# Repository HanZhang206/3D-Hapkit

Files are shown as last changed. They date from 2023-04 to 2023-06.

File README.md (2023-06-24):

<!-- <div align="center"> -->
# **3D Hapkit**: A Low-Cost, Open-Source, 3-DOF Haptic Device Based on the Delta Parallel Mechanism
<div align="center">
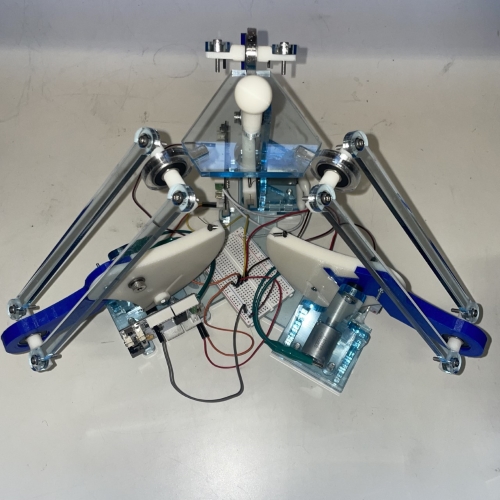
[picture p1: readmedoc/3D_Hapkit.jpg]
3 DOF Hapkit Overview

</div>

The 3D Hapkit is a 3-Degrees-Of-Freedom haptic device that was created as a class project for Haptic Interface Design under Dr. Jeremy Brown in Fall 2022. The 3D Hapkit is based on the [Hapkit 3.0](https://hapkit.stanford.edu/) and was presented as WIP Paper and Demo at [2023 IEEE World Haptics](https://2023.worldhaptics.org/wp-content/uploads/2023/06/1070-doc.pdf). This device is an open-hardware haptic device designed to be low-cost(<$300) and easy to assemble, allowing users to input motions and feel programmed forces in three degrees of freedom. 

Moving forward, the 3D Hapkit will be deployed at the Johns Hopkins University Haptic Interface Design Course in Fall 2023!

<div align="center">


</div>

# **Build One**
## Hardware
<div align="center">
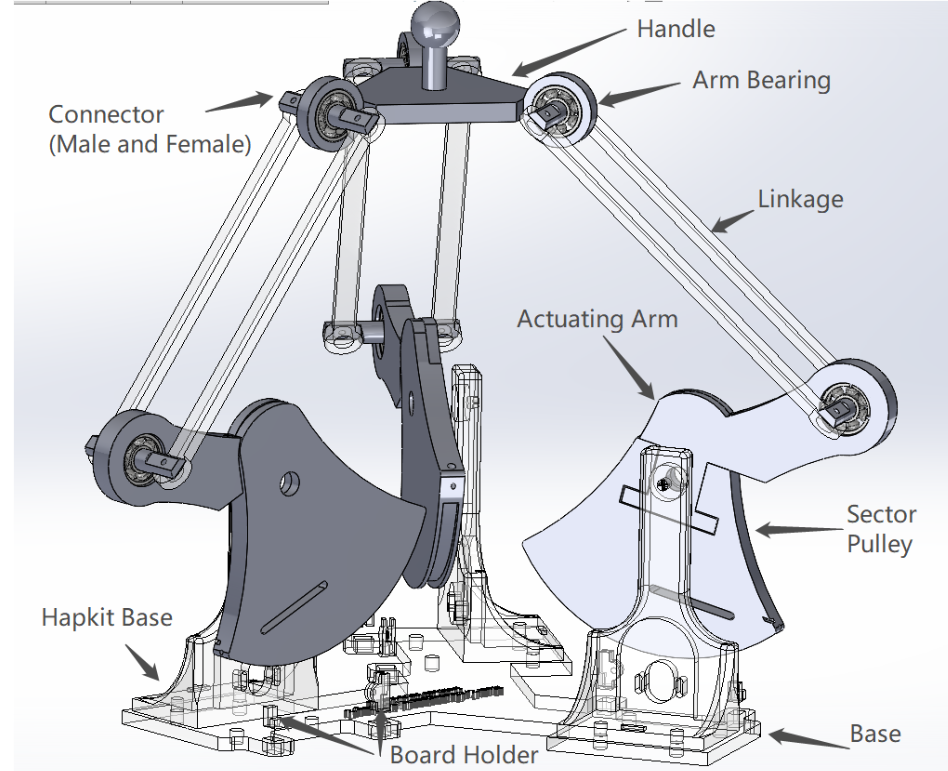
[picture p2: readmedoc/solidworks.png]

</div>  

## Dependency
- [GrabCAD Print Software](https://grabcad.com/print)
- FDM 3D Printer with [ABS filament](https://support.stratasys.com/en/Materials/FDM/ABSplus-P430)/[Soluble Support Material](https://support.stratasys.com/en/Materials/FDM/FDM-Support-Materials)([uPrint SE/uPrint SE Plus](https://support.stratasys.com/en/printers/fdm-legacy/uprint)/[Stratasys F123 Series](https://www.stratasys.com/en/3d-printers/printer-catalog/fdm-printers/f123-series-printers/))
- Laser Cutters([Universal Laser System – VLS6.60](https://www.pdi3d.com/Universal_Laser_VLS6_60_Laser_System_p/ul-vls660.htm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))
- Metric Tap and Die Set(1/4' - 20 & 10-24 & M4)
## Manufacture List
- Parts List: [Here is a parts list with purchase/manufacture information](https://htmlpreview.github.io/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).
- STL files for 3D printing: [Click here to download a zip file of Hapkit STL Files](CAD_and_Manufacturing/3DPrint/3DPrint.zip). Note: Model units are in mm.
- DXF files for laser cutting: [Click here to download a zip file of Hapkit DXF Files](CAD_and_Manufacturing/LaserCut/LaserCut.zip).
- Modifiable SolidWorks files: [Click here to download a zip file of Hapkit SolidWorks Files](CAD_and_Manufacturing/CAD_File/3D-Hapkit.zip). Note: These are only for use with the SolidWorks CAD program.
- Assembly instructions and 3D printing tips: [Here are instructions for assembling your Hapkit into a functional haptic device](readmedoc/assembly.md).

<div align="center">
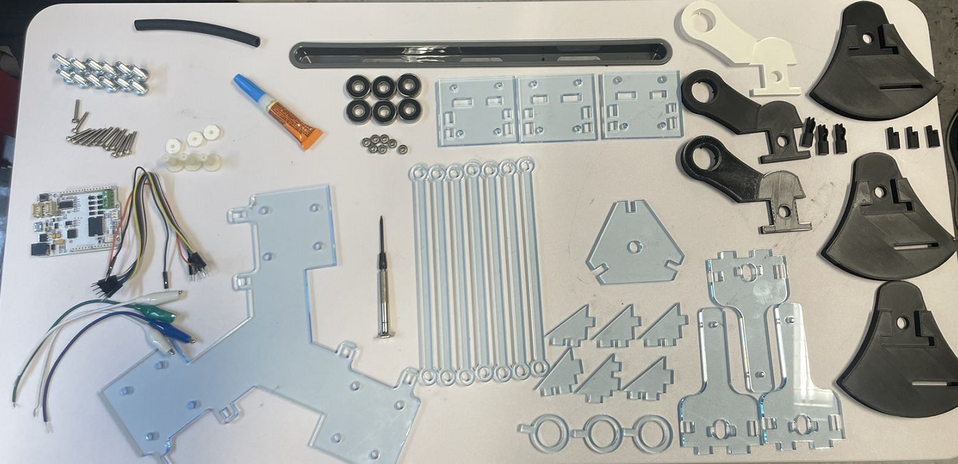
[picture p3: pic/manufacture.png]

</div>

## Electronics 
<div align="center">
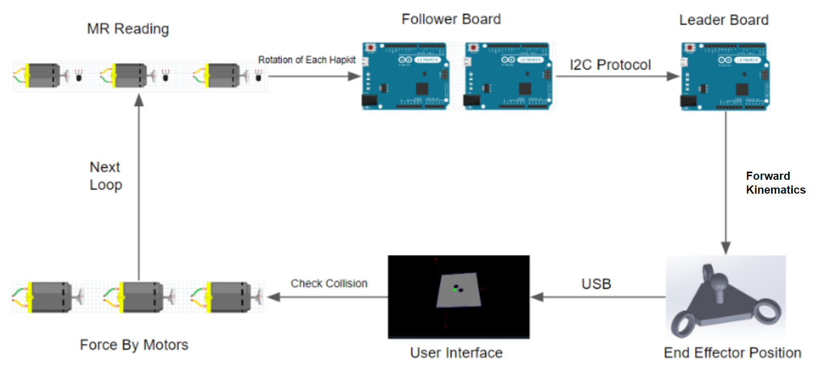
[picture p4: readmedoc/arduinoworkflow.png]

</div>

The electronics of the 3D Hapkit consist of three [Hapkit 3.0s](https://hapkit.stanford.edu/build.html). The Hapkit board can be purchased from [Seeed studio](https://www.seeedstudio.com/depot/hapkit-p-1622.html). It is also possible to manufacture your own PCB by combining an Arduino, motor driver and sensors. Here is a good starting point obtained from Seeed Studio([Files](readmedoc/HapkitSeeedPCB.zip)).

The three boards are communicating using the I2C protocol. We provid sample [Arduino code for follower](3DHapkit_Script/3DHapkit_Follower/3DHapkit_Follower.ino) and [leader](3DHapkit_Script/3DHapkit_Leader/3DHapkit_Learder.ino) to get you started porgramming haptic virtual environments with your 3D Hapkit. The code includes the calculation of forward kinematics and all readings values from sensors.

### To use 
- Connect the ground and I2C pins (A4/A5) of the three boards together.
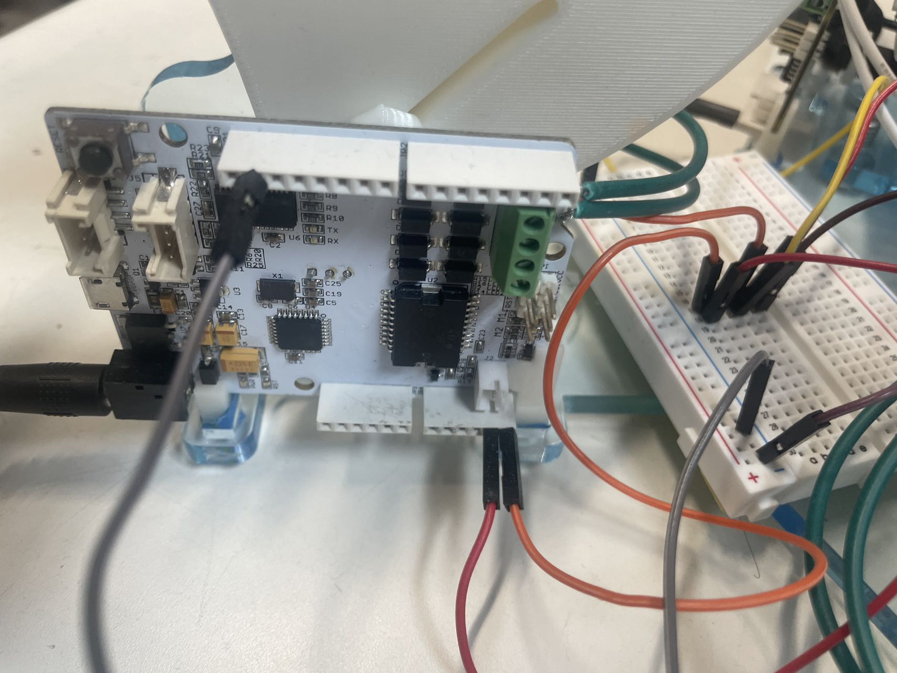
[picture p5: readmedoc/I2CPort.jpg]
  
- Choose one board as the leader and load the script(3DHapkit_Leader.ino).([Arduino IDE Download](https://www.arduino.cc/en/software)).
    - If want to use the serial monitor in the Arduino IDE, comment out **Line 79**(3DHapkit_Leader.ino) in the script:
    ```cpp
  #define PROCESSING 1 //connect to the processing for visualization
    ``` 
- Load the script(3DHapkit_Follower.ino) to two other boards. 
    - In **line 55** (**3DHapkit_Follower.ino**), assign address #8 to follower #1
    ```cpp
  Wire.begin(8);                // join i2c bus with address #8
    ```
    - In **line 58** (**3DHapkit_Follower.ino**), assign address #12 to follower #2
    ```cpp
  Wire.begin(12);                // join i2c bus with address #12
    ```

## Software 
We have created a sample scene for demo purposes. Users are able to control a ball (shown in green) by moving the handle. The ball is rendered in a virtual environment with a virtual surface. Our 3-DOF Hapkit is designed to simulate the virtual surface and render haptic interactions with the surface. Processing ([Download Here](https://processing.org/download)) was used to provide a better visualization.

### To use 
 - Download the [Processing](https://processing.org/download).
 - Open Processing and [deltaProcessing.pde](3DHapkit_Script/deltaProcessing/deltaProcessing.pde).
 - Connect the laptop to the leader board.
 - Check the USB port and change to correct one in **line 38**
     ```cpp
     myPort = new Serial(this, "com5", 115200); //change "com5" based on the local port connection 
      ```
 - Click 'Run'.

<div align="center">
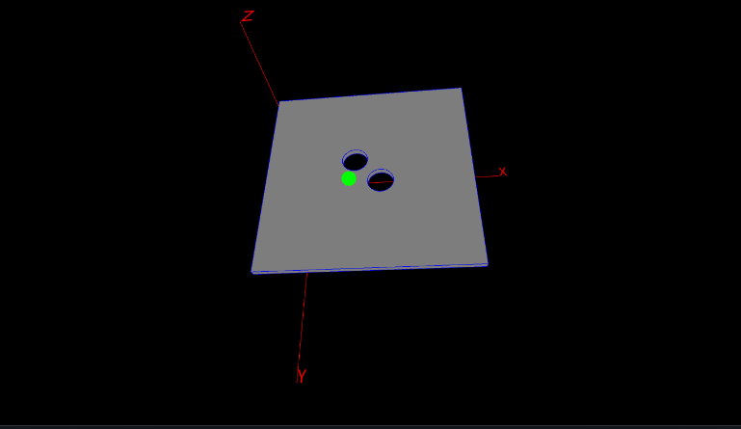
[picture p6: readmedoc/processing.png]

</div>

# **Acknowledgement**
The development and implementation of the 3D Hapkit was supported by the [Haptics and Medical Robotics(HAMR) Laboratory](https://hamr.lcsr.jhu.edu/). Special thanks to Dr. Jeremy Brown for this guidance and invaluable advice.

The 3D Hapkit was made possible by the Hapkit: https://hapkit.stanford.edu/about.html

T. K. Morimoto, P. Blikstein and A. M. Okamura, "[D81] Hapkit: An open-hardware haptic device for online education," 2014 IEEE Haptics Symposium (HAPTICS), Houston, TX, USA, 2014, pp. 1-1, doi: 10.1109/HAPTICS.2014.6775560.

# **Contributors**
 - Han Zhang - MSE in Biomedical Engineering, Johns Hopkins University
 - Jan Bartels - MSE in Robotics, Johns Hopkins University
 - Yuting Zhang - MSE in Computer Science, Johns Hopkins University

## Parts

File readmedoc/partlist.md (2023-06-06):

| **Component** | **3D Model** | **Quanitity** | **Manufacture Method** | **Material** | **Cost** | 
| :-----| :----: | :----: | :----: | :----: | :----: |
| Base | | 1 |Laser Cutter | 15/64" Cast Acrylic | ~ | 
| Linkage |  | 6 |Laser Cutter | 15/64" Cast Acrylic | ~ | 
| Handle |  | 1 |Laser Cutter | 15/64" Cast Acrylic | ~ | 
| 1-Dof Hapkit Base |  | 3 |Laser Cutter | 15/64" Cast Acrylic | ~ | 
| 3D Hapkit Sector Pulley |  | 3 |FDM 3D Printing  | ABS | ~ | 
| Actuating Arm |  | 3 |FDM 3D Printing  | ABS | ~ | 
| 3D Printed Connector(Male) |  | 6 |FDM 3D Printing  | ABS  | ~ | 
| 3D Printed Connector(Female) |  | 6 |FDM 3D Printing  | ABS  | ~ | 
| 3D Printed Tightening Washer |  | 3 |FDM 3D Printing  | ABS  | ~ | 
| 3D Printed Drive Wheel/Magnet Holder |  | 3 |FDM 3D Printing  | ABS  | ~ | 
| Broad Holder 1 |  | 3 |FDM 3D Printing  | ABS  | ~ | 
| Broad Holder 2 |  | 3 |FDM 3D Printing  | ABS  | ~ | 
| Connection Bearing 3mm * 8mm * 4mm |  | 12 |Purchased from [Amazon](https://www.amazon.com/Bearing-Shielded-Bearings-Performance-Effective/dp/B092Z2QB6X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) | Alloy Steel | $9.20 for 20 Pack 623ZZ Ball Bearing | 
| Arm Bearing 8mm * 22mm * 7mm |  | 12 |Purchased from [Amazon](https://www.amazon.com/Industrial-8x22x7mm-Bearings-Pre-Lubricated-Skateboards/dp/B09S5Z5J5L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) | Alloy Steel | 2 * $10.99 (4 Pack 608-2RS Ball Bearing)| 
| Screws (for capstan adjustment) size 4-40, 3/4" length  |  | 3 | Purchased from Mcmaster-Carr(Part ID: 91781A113) | 18-8 Stainless Steel |  $6.78 per pack of 100 | 
| Pan Head Phillips Screws(for Hapkit installation),¼-20 3/4 |  | 12 |Purchased from Mcmaster-Carr(Part ID:91772A540) | 18-8 Stainless Steel | $18.85 per pack of 50 | 
| Pan Head Phillips Screws(for bearing installation),M4 x 0.7mm Thread, 16mm Long |  | 12 |Purchased from Mcmaster-Carr(Part ID:92000A226) | 18-8 Stainless Steel | $10.85 per pack of 50 | 
|Neoprene tubing, 1/4" inner diameter, 3/8" outer diameter, cut to 3/4" length |  | 3 |Purchased from Mcmaster-Carr(Part ID:51075K27) | Neoprene | $12.2 for a 10'-long tube ($1.22 per foot) | 
| Bearing: SAE 863 bronze flanged sleeve bearing |  | 3 |Purchased from Mcmaster-Carr(Part ID: 2938T3) | 863 Iron-Copper | 3 * $0.92 | 
| Stainless Steel Thread-Locking Shoulder Screw, 1/4" Diameter x 5/8" Long Shoulder, 10-24 Thread |  | 3 | Purchased from Mcmaster-Carr(Part ID: 90311A144) | Stainless Steel | 3 * $6.01 | 
| Shaft collar |  | 3 |Purchased from Mcmaster-Carr(Part ID: 9414T6) | Black-oxide steel | 3 * $1.55 | 
| Screws for the motor  |  | 6 |Purchased from Mcmaster-Carr(Part ID: 91735A104) | 316 Stainless Steel | $4.59 For a Pack of 50 | 
| Washers for motor |  | 6 |Purchased from Mcmaster-Carr(Part ID: 92150A101) | Nylon Plastic | $10.20 For a Pack of 100 | 
| Nylon Coated Stainless Steel Wire Rope |  | 3 |Purchased from Mcmaster-Carr(Part ID: 8930T16)| 18-8 Stainless Steel | $10.00 For 25 feet | 
| Zinc - Plated Copper Oval Compression Sleeve |  | 3 |Purchased from Mcmaster-Carr(Part ID: 3898T29) | Zinc-Plated Copper | $2.63 For a Pack of 50 | 
| Zinc -Plated Steel Machine Screw Hex Nut |  | 3 |Purchased from Mcmaster-Carr(Part ID: 90480A005) | Zinc-Plated Copper | $1.05 For a Pack of 100 | 
| Motor |  | 3 |Purchased from Jameco(Part ID: 238473) | Motor | 3 * $5.95 | 
| Magnet |  | 3 |Purchased from Jameco(Part ID: 57295K73) | Alnico | 3 * $2.38 | 
| Magnetoresistive sensor|  | 3 |Purchased from DigiKey (Part ID:568-8399-1-ND) | Magnet Sensor | 3 * $6.73  | 
| Hapkit board |  | 3 |Purchased from Seeed Studio(Part ID :KIT04300M) | Hapkit Board | 3 * $35 | 
| Power supply for Hapkit board |  | 3 |Purchased from Pololu (Part ID: 1471) | Power Supply | 3 * $7.95 | 
| Leads with alligator clips on both ends |  | 3 |Purchased from Mouser(Part ID: 474-CAB-14303) | Alligator Clips | $7.57 | 
| USB cable for communication |  | 1 |Purchased from Monoprice(Part ID: 4867) | Cable  | $1.49 | 

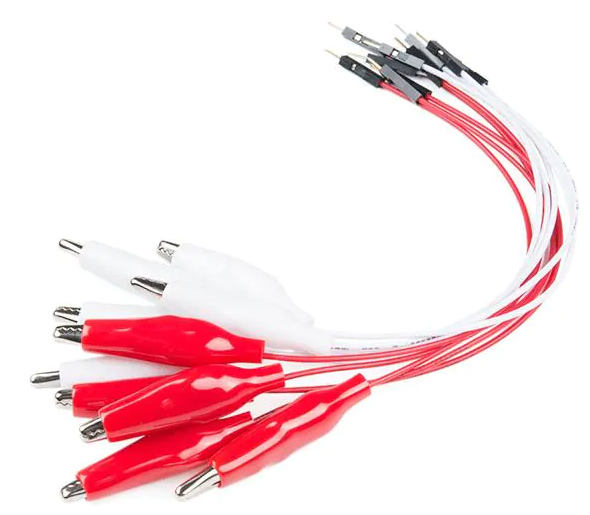
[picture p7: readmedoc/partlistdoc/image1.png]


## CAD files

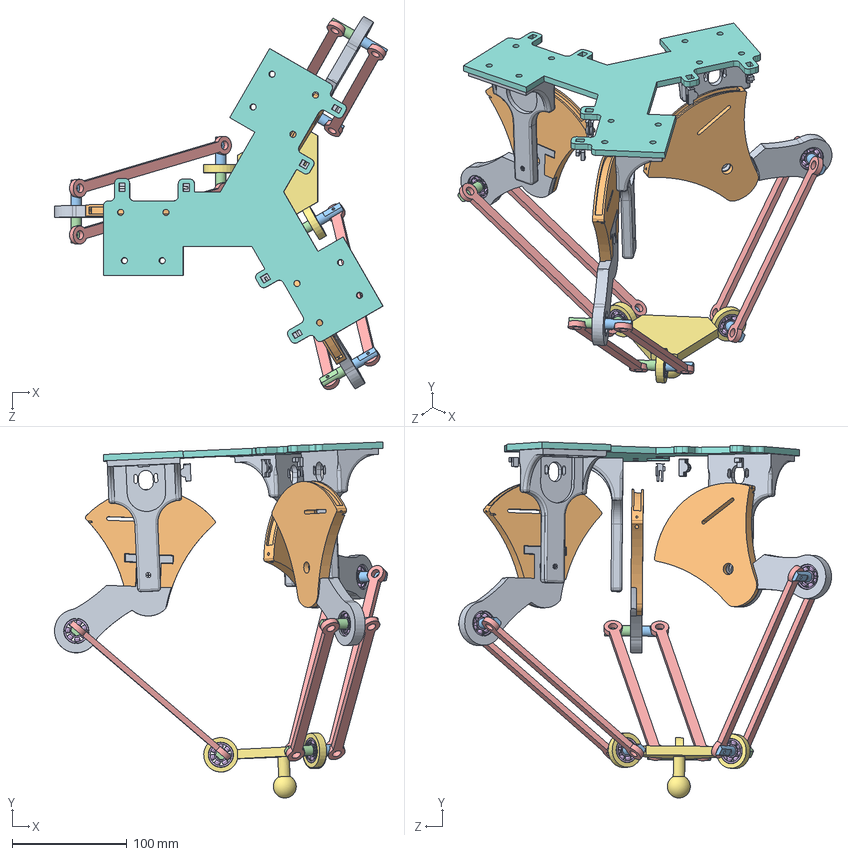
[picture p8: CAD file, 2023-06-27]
CAD_and_Manufacturing/CAD_File/3D-Hapkit.SLDASM
290.2 x 310.1 x 325.1 mm
Hapkit3_0_Base x 3
Hapkit Sector Pulley x 3
Connector_Male x 6
Connector_Female x 6
Linkage x 6
608-2RS.step x 6
handle
base
Actuating Arm x 3

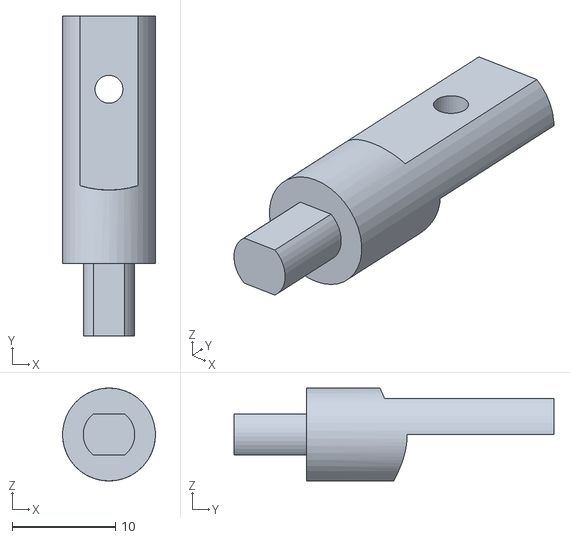
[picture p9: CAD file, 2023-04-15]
CAD_and_Manufacturing/3DPrint/Connector_MaleX6.STL
9.00 x 31.0 x 9.00

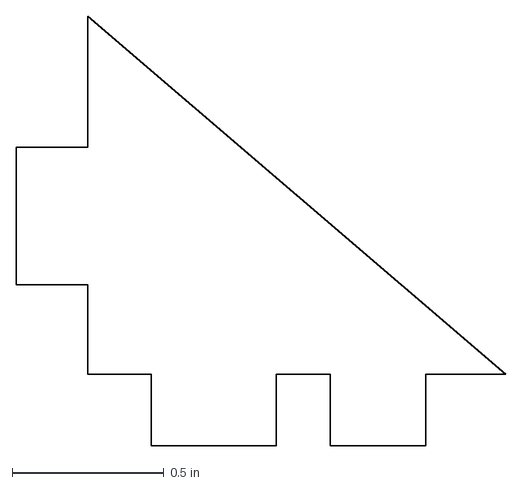
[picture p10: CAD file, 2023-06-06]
CAD_and_Manufacturing/LaserCut/support2X3.DXF
1.61 x 1.42 in

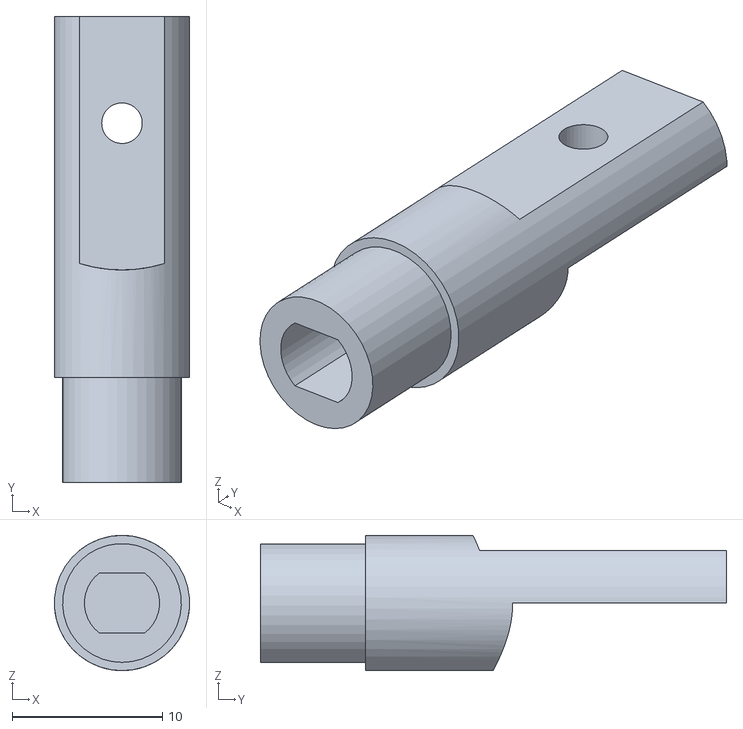
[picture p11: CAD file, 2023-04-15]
CAD_and_Manufacturing/3DPrint/Connector_FemaleX6.STL
9.00 x 31.0 x 9.00

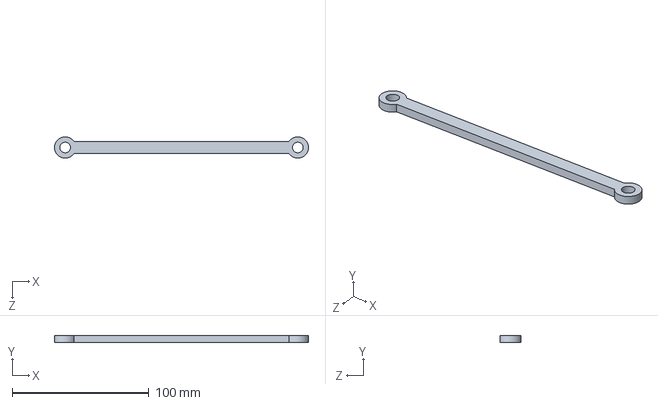
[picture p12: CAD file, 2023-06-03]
CAD_and_Manufacturing/CAD_File/Linkage.SLDPRT
185.6 x 5.00 x 15.6 mm

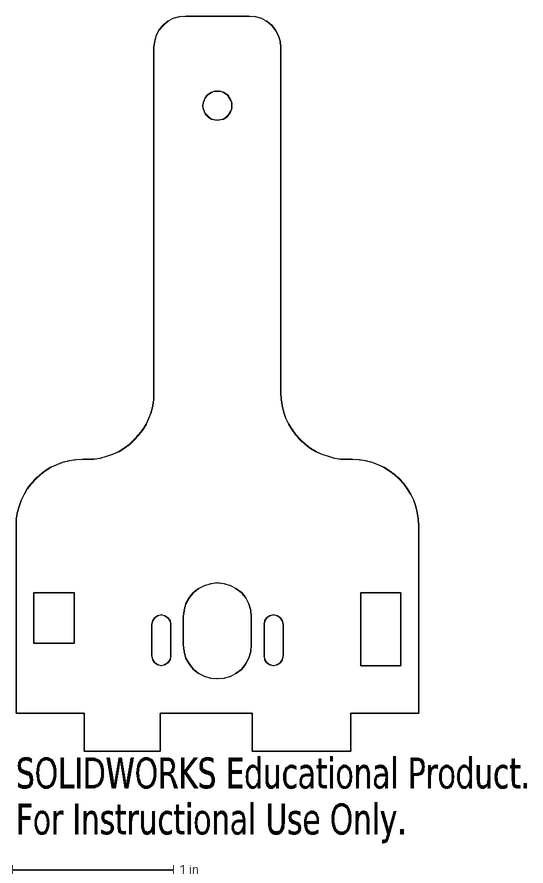
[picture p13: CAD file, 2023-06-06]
CAD_and_Manufacturing/LaserCut/standX3.DXF
SOLIDWORKS Educational Product.
For Instructional Use Only.

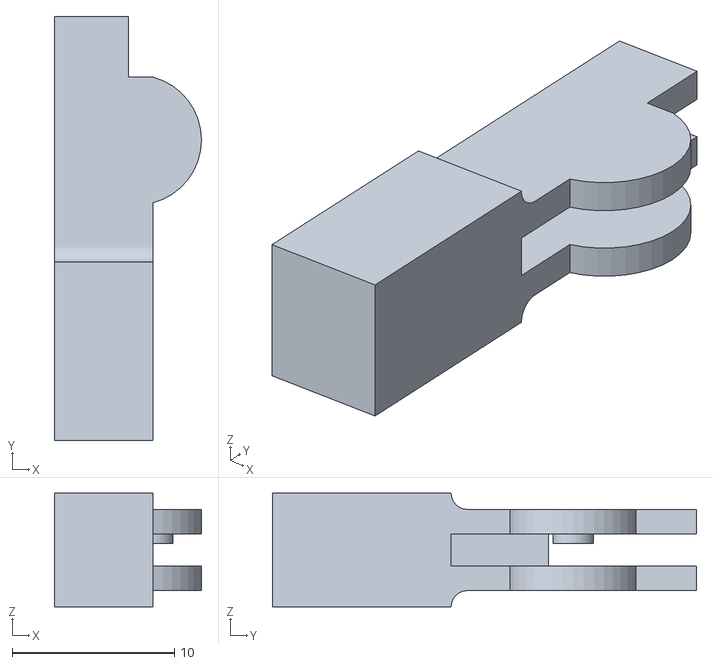
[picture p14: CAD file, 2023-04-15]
CAD_and_Manufacturing/3DPrint/printx_2X3.STL
9.05 x 26.1 x 7.00

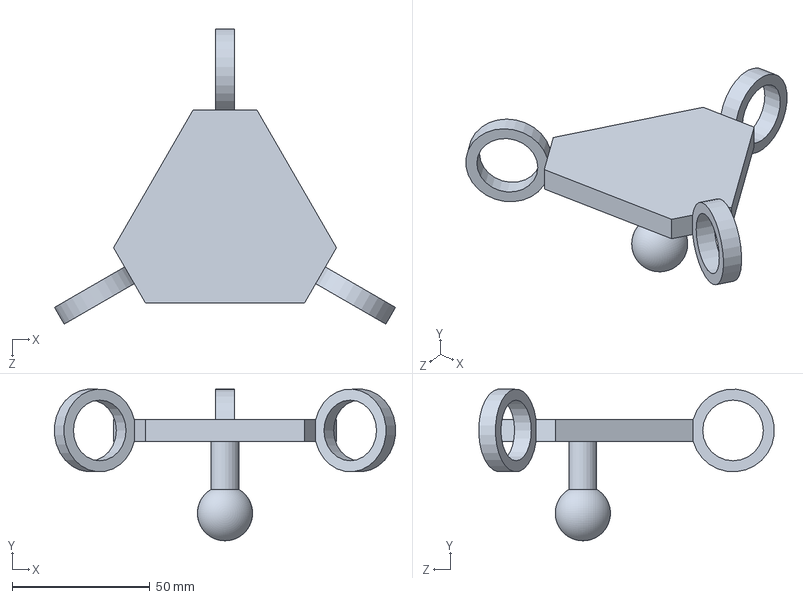
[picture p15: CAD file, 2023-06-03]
CAD_and_Manufacturing/CAD_File/handle.SLDPRT
123.6 x 55.0 x 107.1 mm

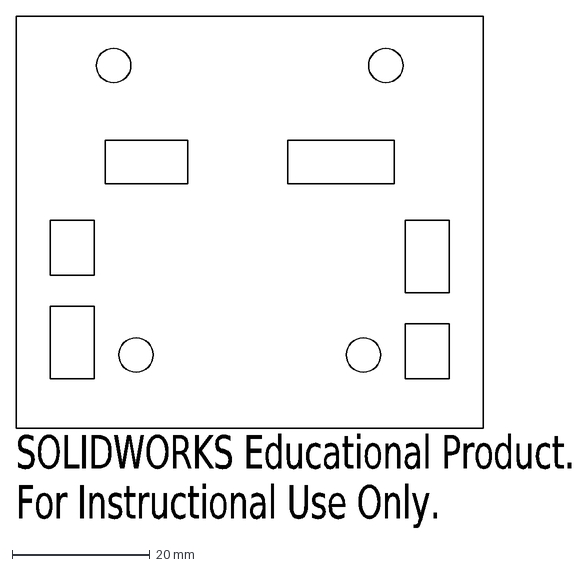
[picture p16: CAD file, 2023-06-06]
CAD_and_Manufacturing/LaserCut/handleX3.DXF
SOLIDWORKS Educational Product.
For Instructional Use Only.

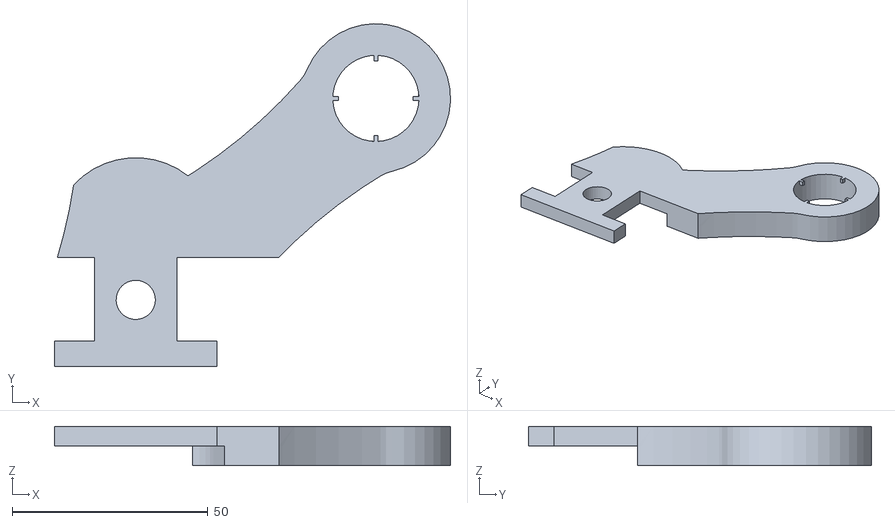
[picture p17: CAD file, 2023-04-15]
CAD_and_Manufacturing/3DPrint/Actuating ArmX3.STL
101.1 x 87.4 x 10.00

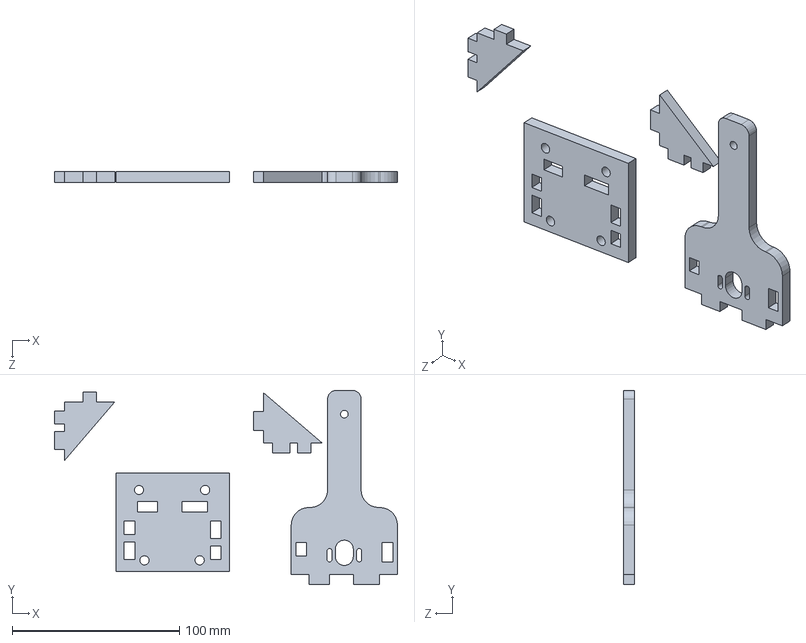
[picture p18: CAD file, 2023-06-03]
CAD_and_Manufacturing/CAD_File/LaserCut_Frame.SLDPRT
204.9 x 115.9 x 6.35 mm

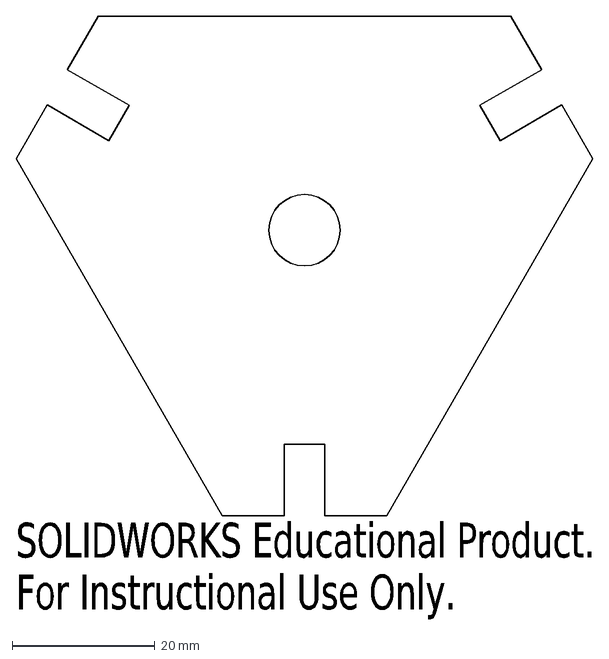
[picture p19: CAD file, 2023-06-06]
CAD_and_Manufacturing/LaserCut/handleX1.DXF
SOLIDWORKS Educational Product.
For Instructional Use Only.

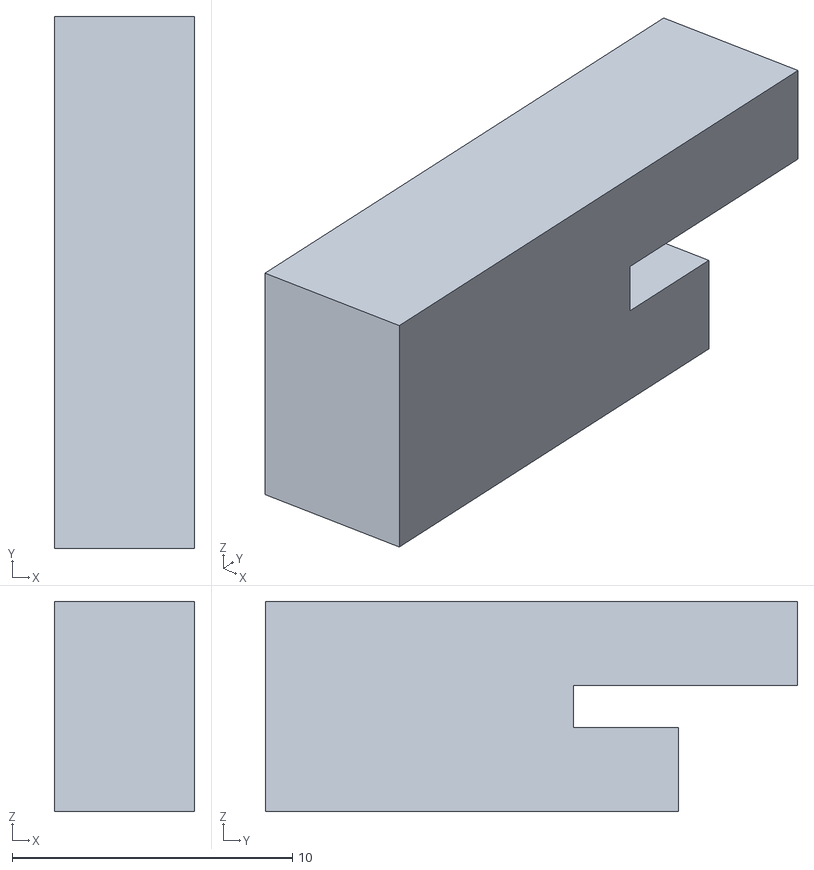
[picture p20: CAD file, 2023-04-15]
CAD_and_Manufacturing/3DPrint/print_1X3.STL
5.00 x 19.0 x 7.50

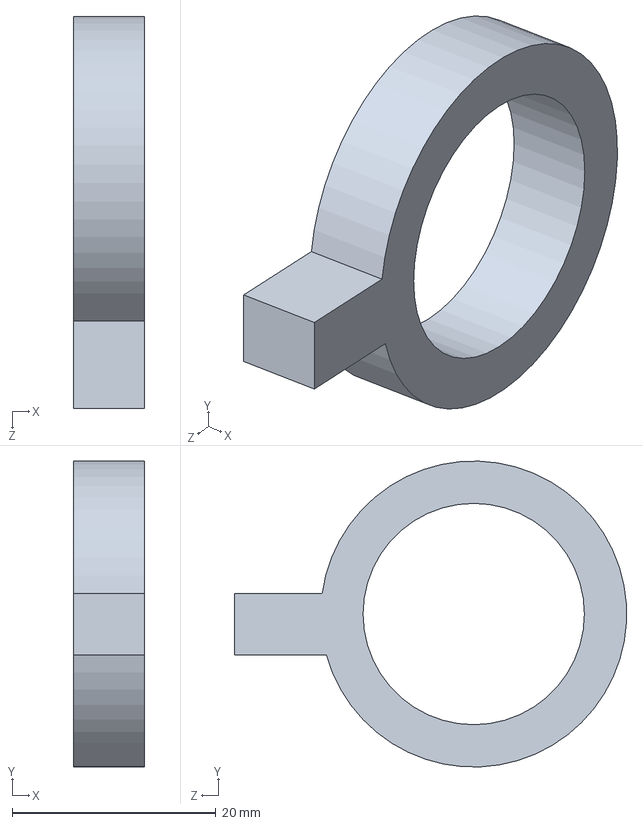
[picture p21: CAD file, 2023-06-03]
CAD_and_Manufacturing/CAD_File/handle_lasercut.SLDPRT
7.00 x 30.0 x 38.4 mm

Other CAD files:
CAD_and_Manufacturing/LaserCut/baseX1.DXF
CAD_and_Manufacturing/3DPrint/Hapkit Sector PulleyX3.STL
CAD_and_Manufacturing/CAD_File/broadholder1.SLDPRT
CAD_and_Manufacturing/LaserCut/support1X3.DXF
CAD_and_Manufacturing/3DPrint/Drive_WheelX3.STL
CAD_and_Manufacturing/3DPrint/print_2X3.STL
CAD_and_Manufacturing/CAD_File/608-2RS.step.SLDPRT
CAD_and_Manufacturing/CAD_File/Actuating Arm.SLDPRT
CAD_and_Manufacturing/CAD_File/Connector_Female.SLDPRT
CAD_and_Manufacturing/CAD_File/Connector_Male.SLDPRT
CAD_and_Manufacturing/CAD_File/Drive_Wheel.SLDPRT
CAD_and_Manufacturing/CAD_File/Hapkit Sector Pulley.SLDPRT
CAD_and_Manufacturing/CAD_File/Hapkit3_0_Base.SLDPRT
CAD_and_Manufacturing/CAD_File/Tightening Washer.SLDPRT
CAD_and_Manufacturing/CAD_File/base.SLDPRT
CAD_and_Manufacturing/CAD_File/broadholder2.SLDPRT
CAD_and_Manufacturing/CAD_File/tophandle.SLDPRT
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

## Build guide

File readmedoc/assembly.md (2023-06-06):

# Assembly Instructions
 -  Obtain the all Hapkit components by purchasing, 3d printing and laser cutting
    
 - Gather the 10-24, 1/4in - 20 , and M4 tap and tap handle
 - Tap the thread for those parts

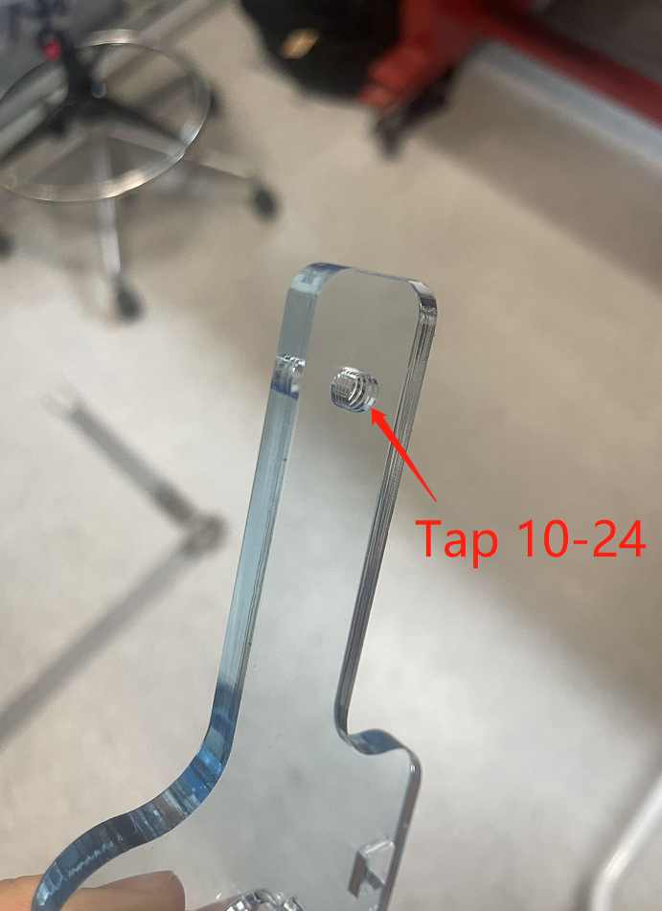
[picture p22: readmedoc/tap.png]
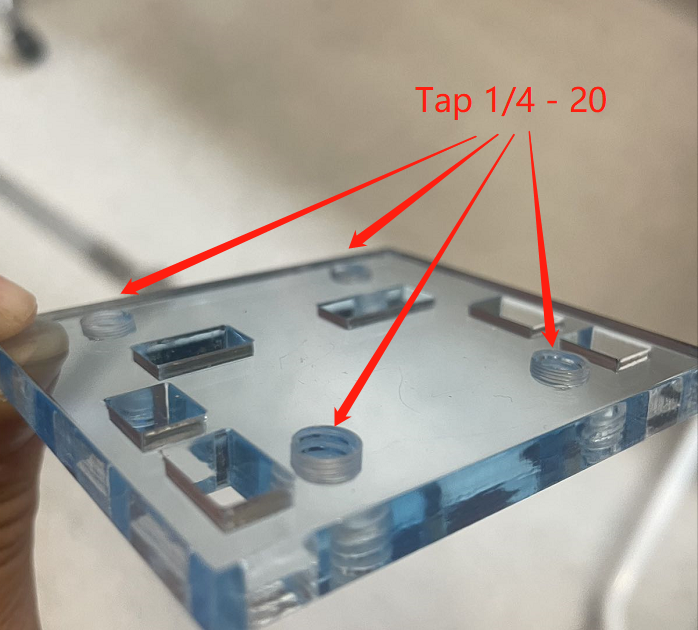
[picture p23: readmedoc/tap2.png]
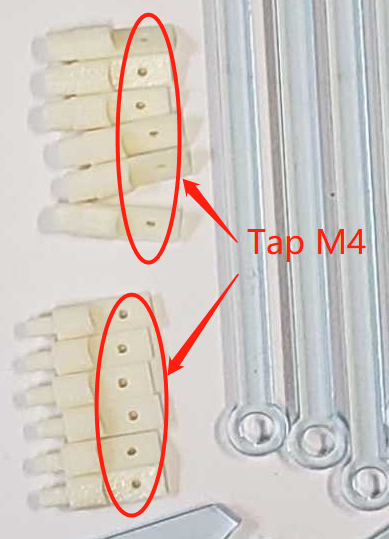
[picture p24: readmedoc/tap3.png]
    
 - Install the base and stands with screws

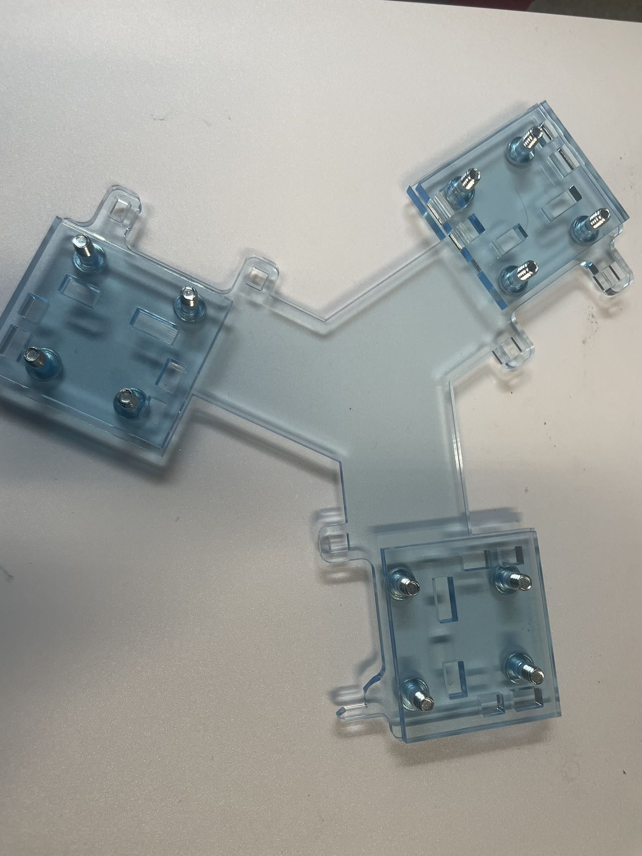
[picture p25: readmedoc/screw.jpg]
    
 - Assemble the parts by using super glue 

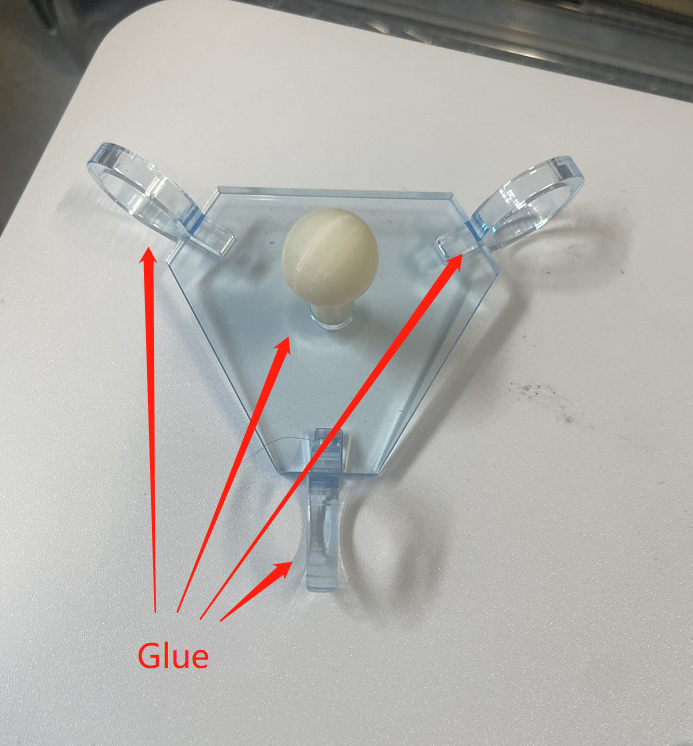
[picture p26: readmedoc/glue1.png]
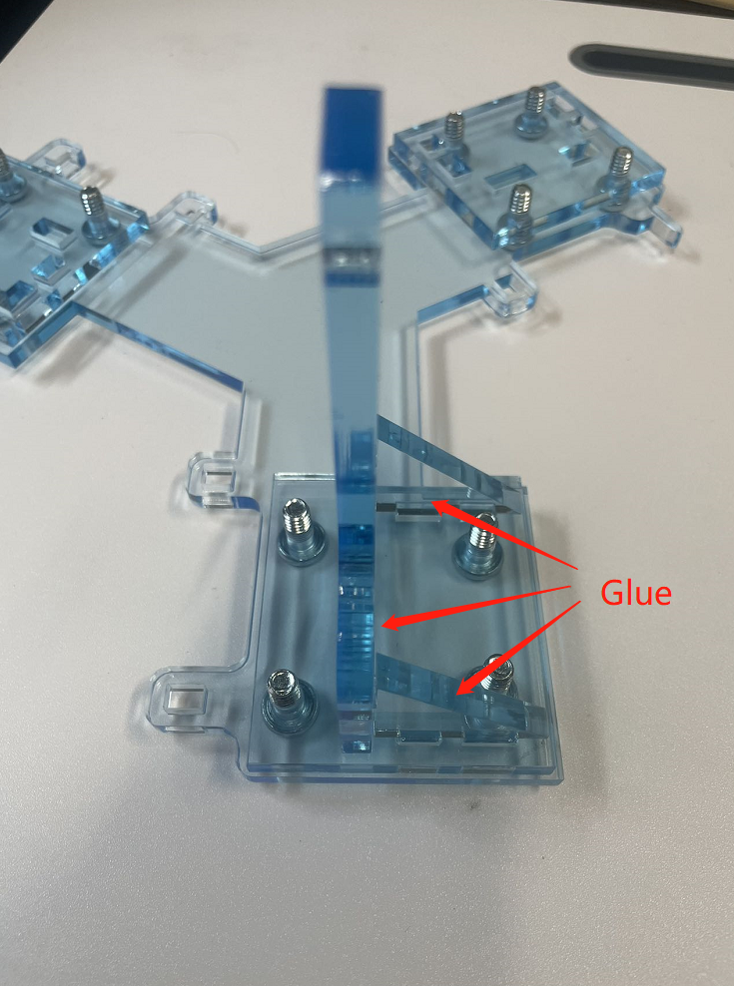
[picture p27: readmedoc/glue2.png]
    
 - Assemble the device 
    - The detail of Hapkit assembly instructions can be found [here](https://hapkit.stanford.edu/files/HapkitAssemblyInstructions_v11_11_15.pdf)
    
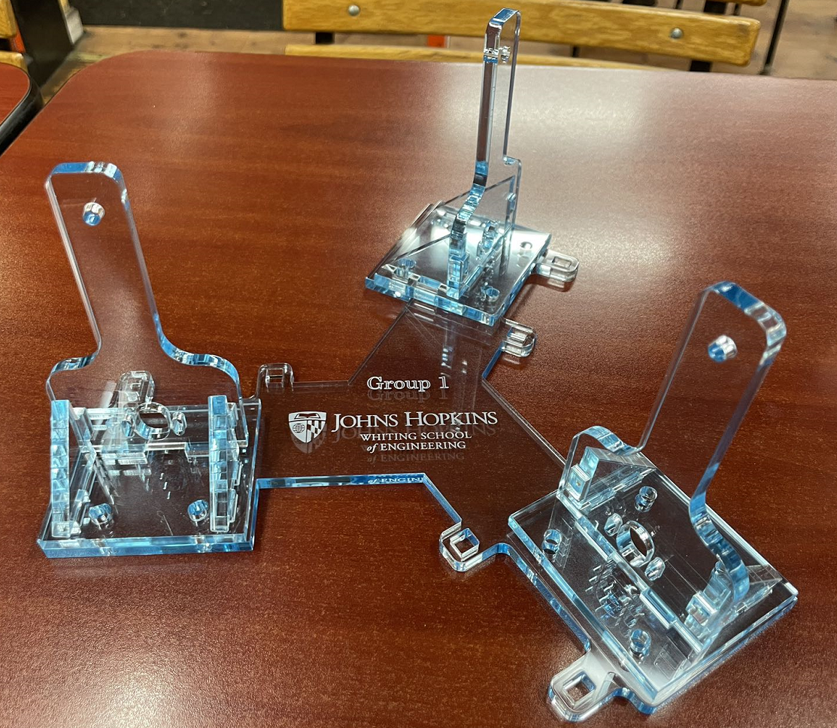
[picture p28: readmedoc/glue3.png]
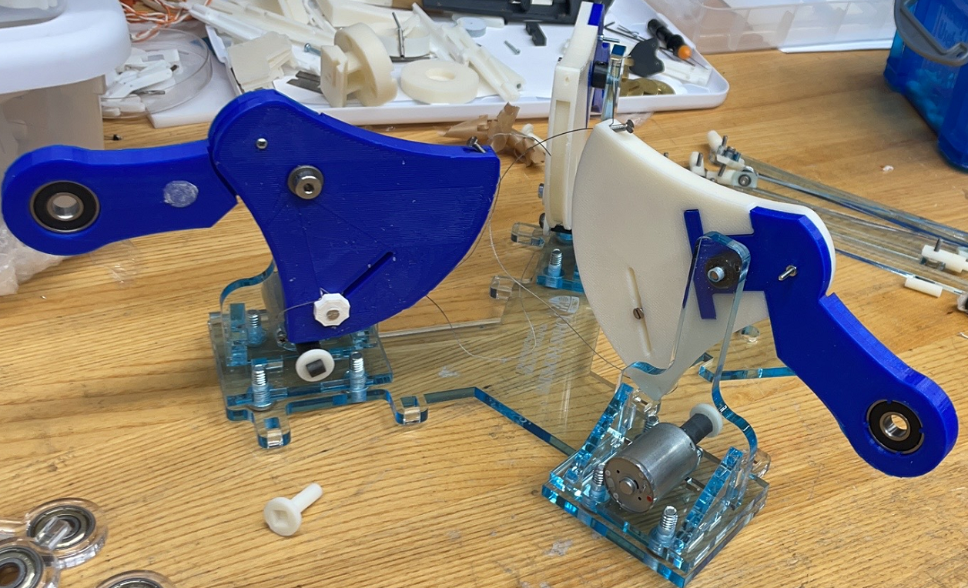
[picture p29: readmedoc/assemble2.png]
    
    
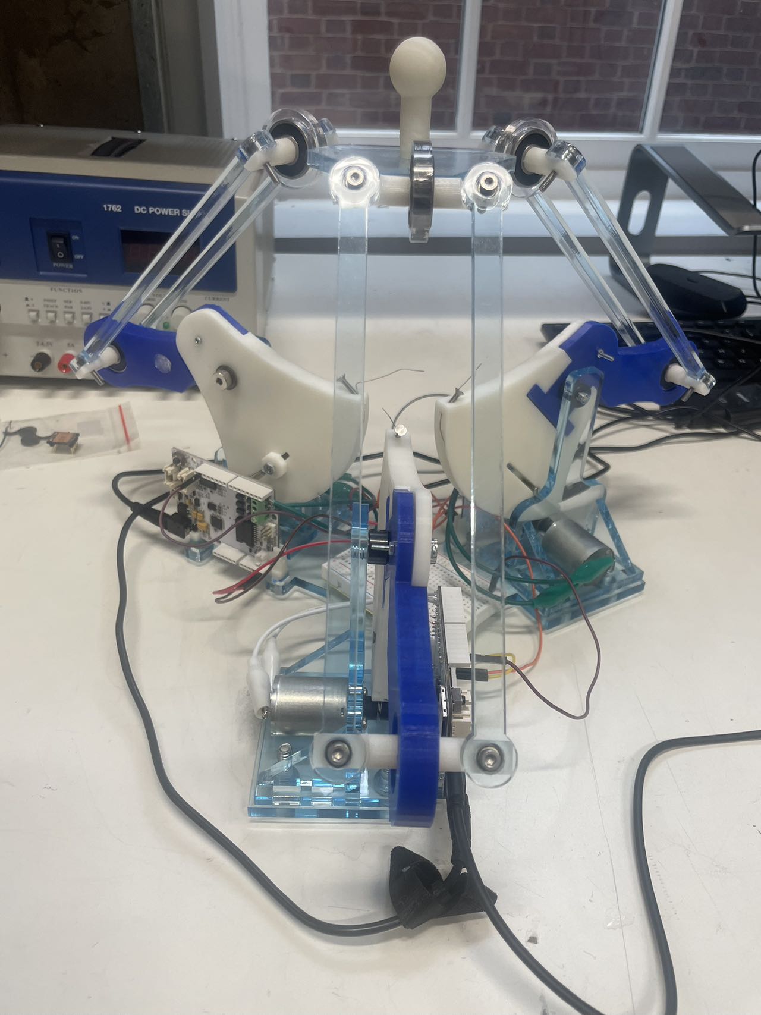
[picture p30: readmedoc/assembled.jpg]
    
# 3D Printing Tip
- Import the cad files into the [GrabCAD Print software](https://grabcad.com/print).
- Position parts to the desired orientation to optimize printability and minimize material usage like below.
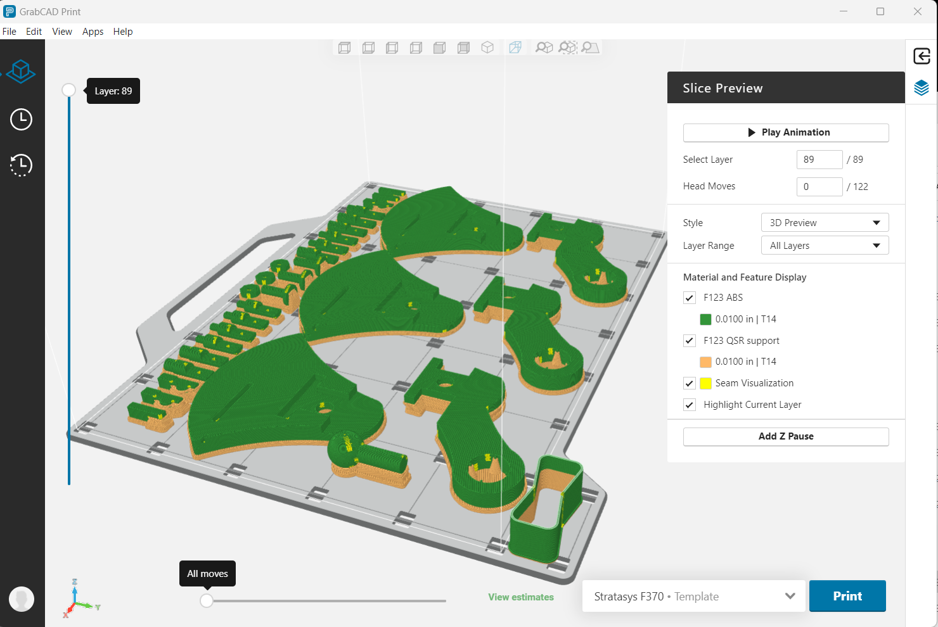
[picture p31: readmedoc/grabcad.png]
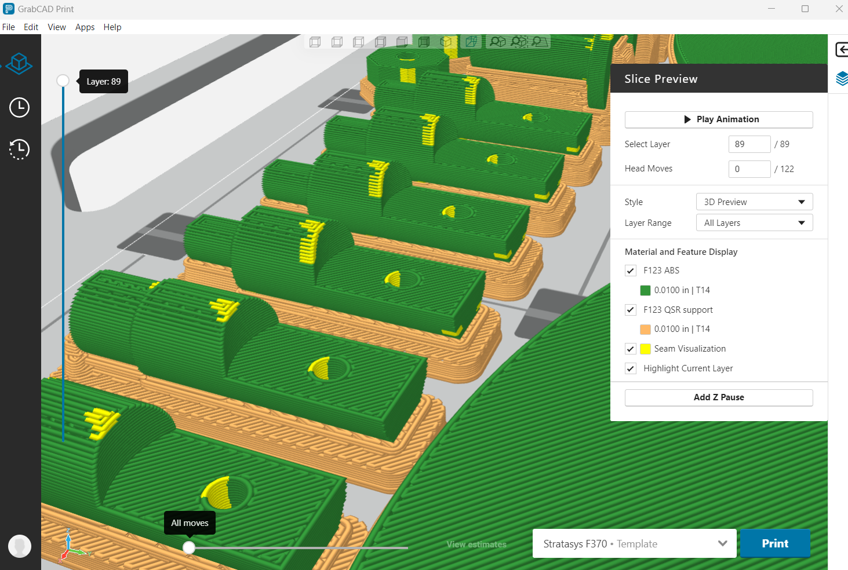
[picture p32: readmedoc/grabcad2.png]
    
- Upload print file to FDM printer and print using a clean build platform with [ABS filament](https://support.stratasys.com/en/Materials/FDM/ABSplus-P430) and [Soluble Support Material](https://support.stratasys.com/en/Materials/FDM/FDM-Support-Materials). 

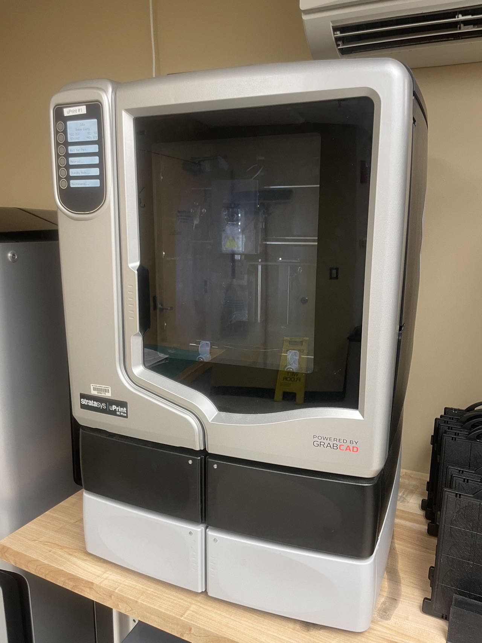
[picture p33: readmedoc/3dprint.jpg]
    
- Once the print has finished, all parts were washed with mild NaOH for 3 hours to ensure all supported material was removed.

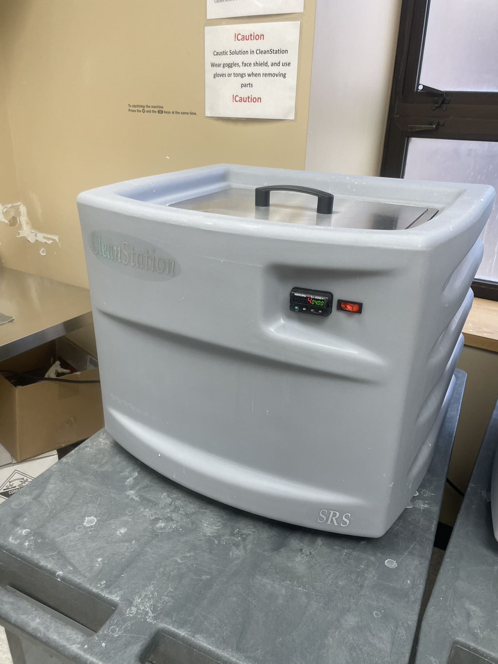
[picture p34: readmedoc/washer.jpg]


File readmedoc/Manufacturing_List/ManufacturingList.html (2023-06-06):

Component | 3D Model | Quantity | Manufacture Method | Material | Cost
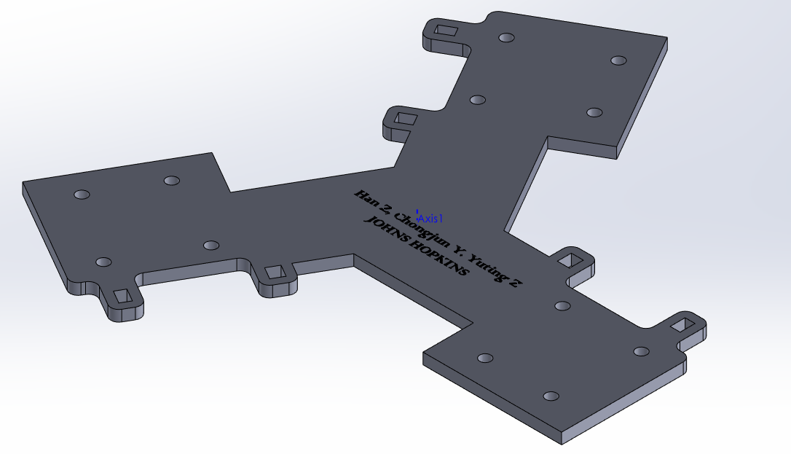
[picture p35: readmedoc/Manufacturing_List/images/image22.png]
Base |  | 1 | Laser Cutter | 15/64" Cast Acrylic | $7.78
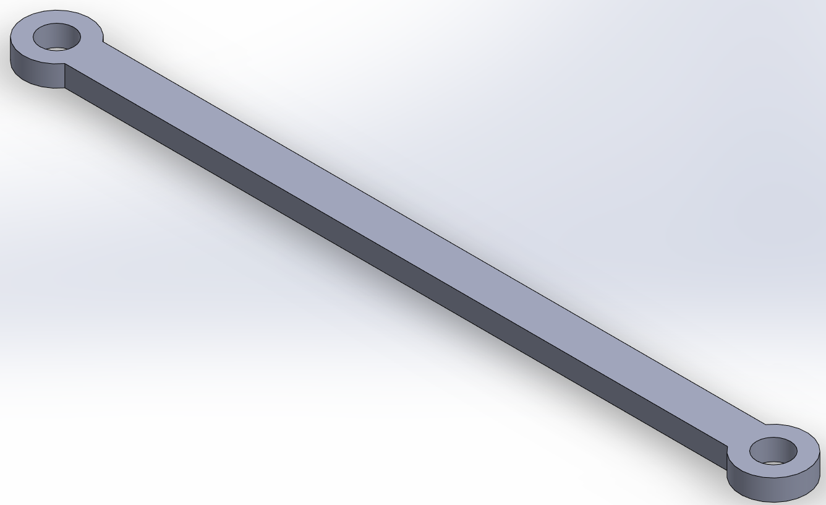
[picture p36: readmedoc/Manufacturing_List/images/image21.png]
Linkage |  | 6 | Laser Cutter | 15/64" Cast Acrylic | $2.77
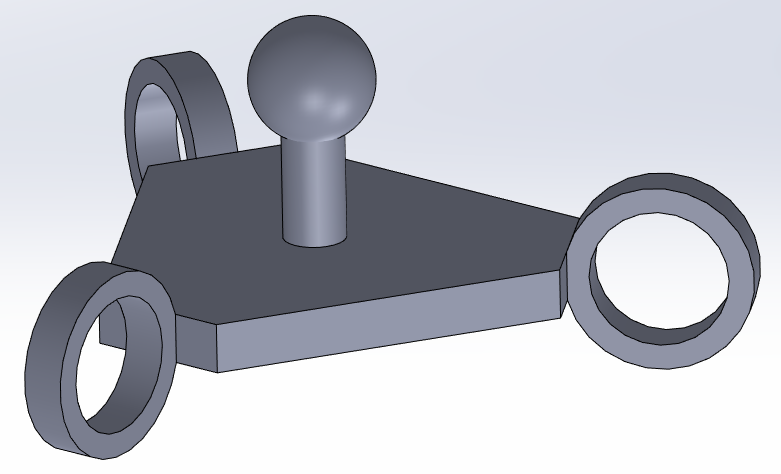
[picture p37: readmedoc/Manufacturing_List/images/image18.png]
Handle |  | 1 | Laser Cutter | 15/64" Cast Acrylic | $2.37
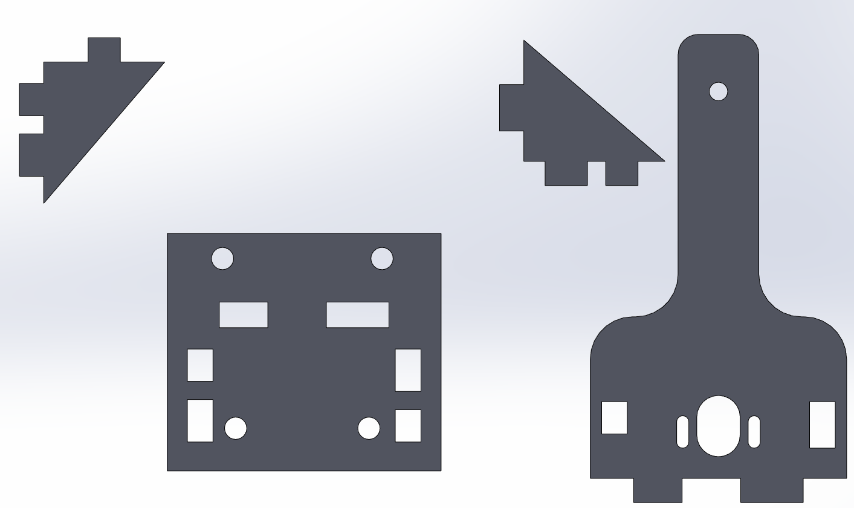
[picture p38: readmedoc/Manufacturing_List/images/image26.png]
1-Dof Hapkit Base |  | 3 | Laser Cutter | 15/64" Cast Acrylic | 3*$3.13
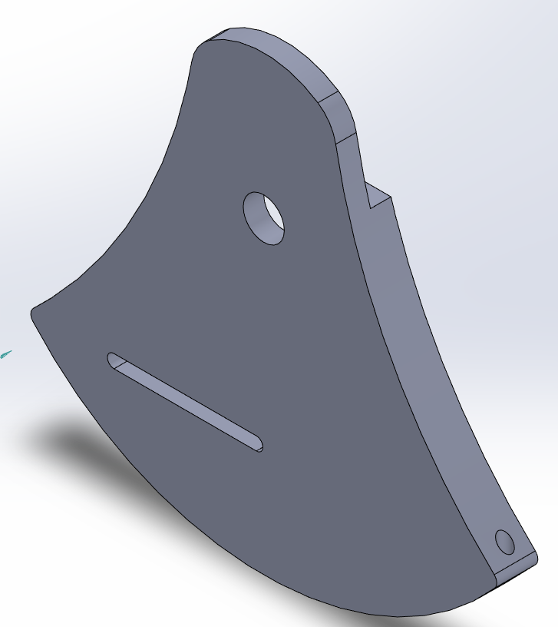
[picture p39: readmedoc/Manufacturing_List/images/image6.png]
3D Hapkit Sector Pulley |  | 3 | FDM 3D Printing | ABS | All part will be printed by using UPrint SE Plus with ABS and dissolvable support material. The total weight of plastic used is about 300 grams.
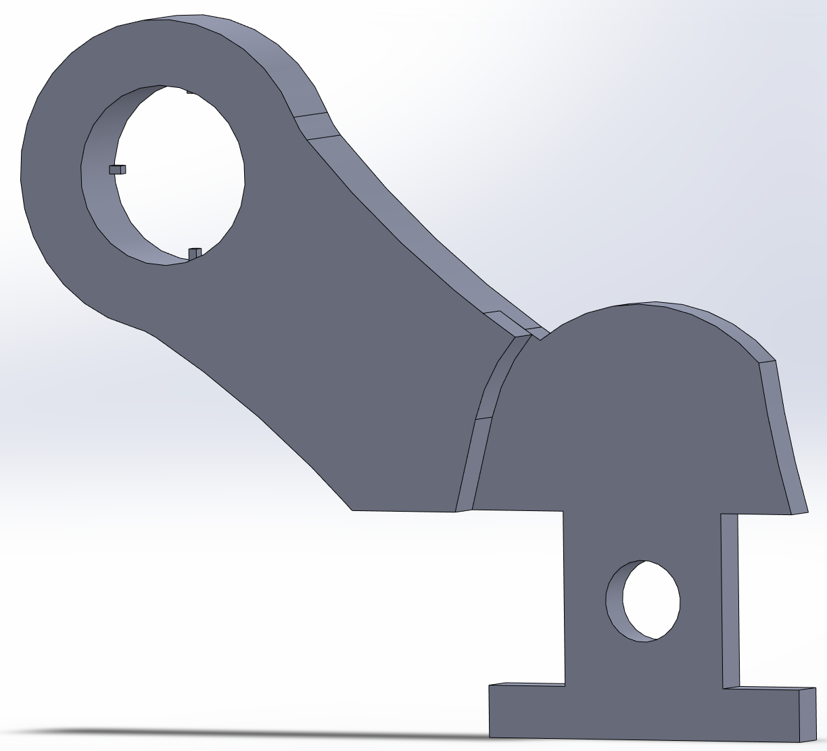
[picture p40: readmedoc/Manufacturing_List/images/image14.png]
3D Printed Actuating Arm |  | 3 | FDM 3D Printing | ABS
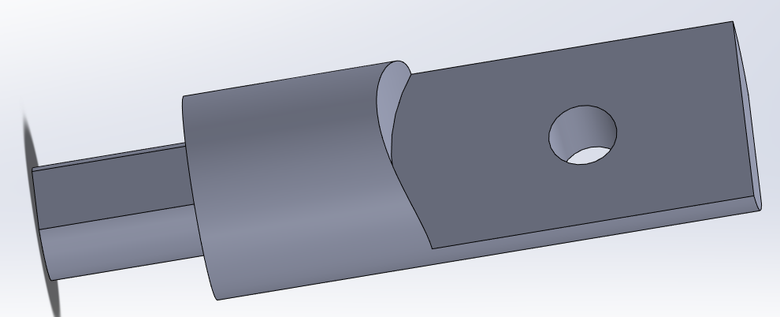
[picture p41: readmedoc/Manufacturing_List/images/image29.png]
3D Printed Connector(Male) |  | 6 | FDM 3D Printing | ABS
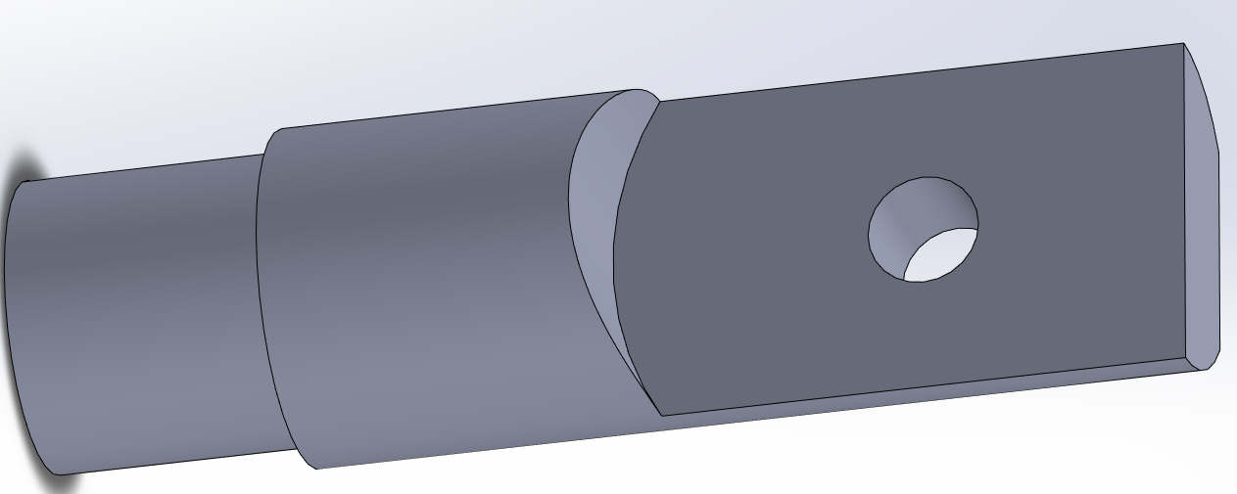
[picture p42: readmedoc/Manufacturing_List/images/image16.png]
3D Printed Connector(Female) |  | 6 | FDM 3D Printing | ABS
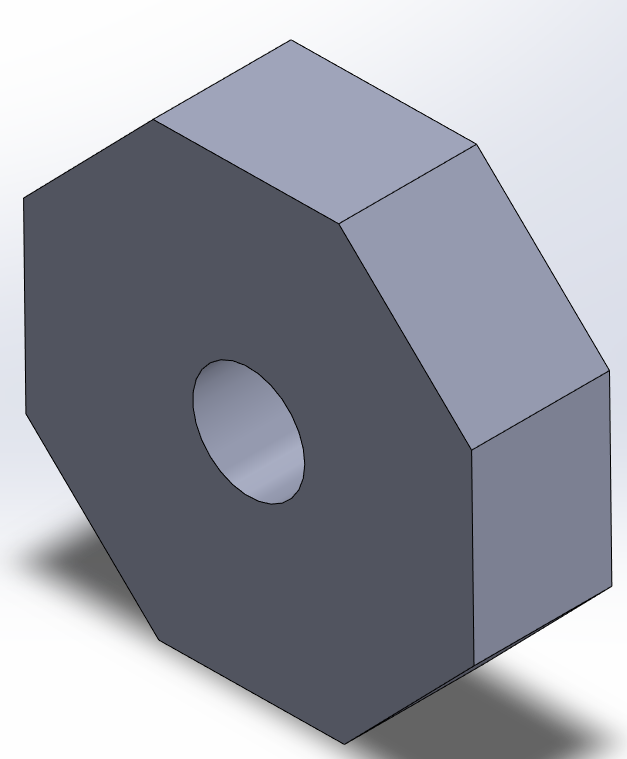
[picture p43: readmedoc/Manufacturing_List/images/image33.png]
3D Printed Tightening Washer |  | 3 | FDM 3D Printing | ABS
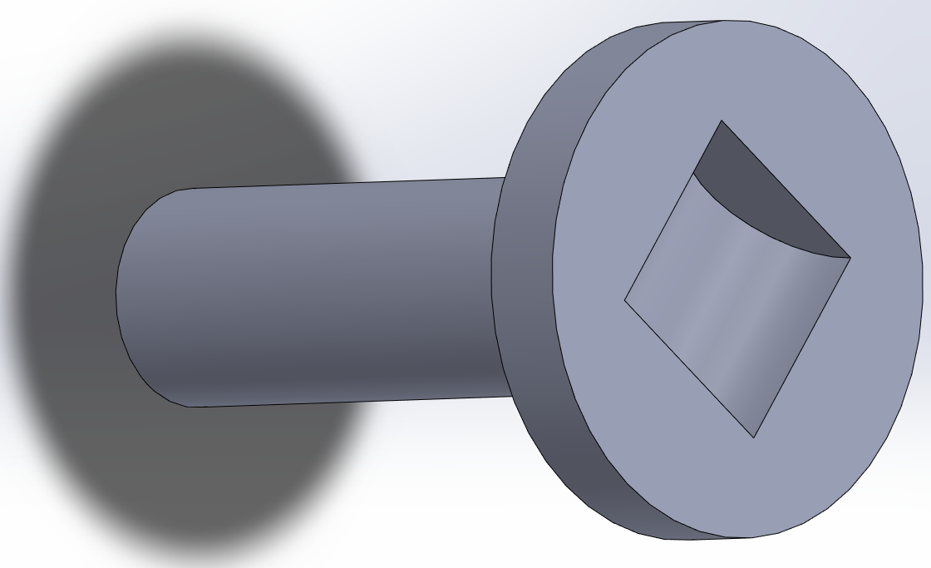
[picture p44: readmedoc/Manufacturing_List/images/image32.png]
3D Printed Drive Wheel/Magnet Holder |  | 3 | FDM 3D Printing | ABS
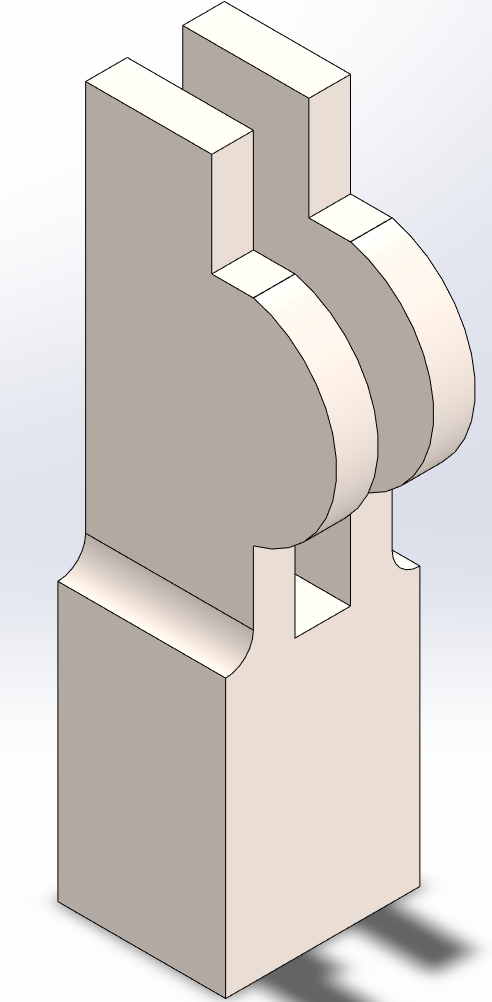
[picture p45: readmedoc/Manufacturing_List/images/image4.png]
Broad Holder 1 |  | 3 | FDM 3D Printing | ABS
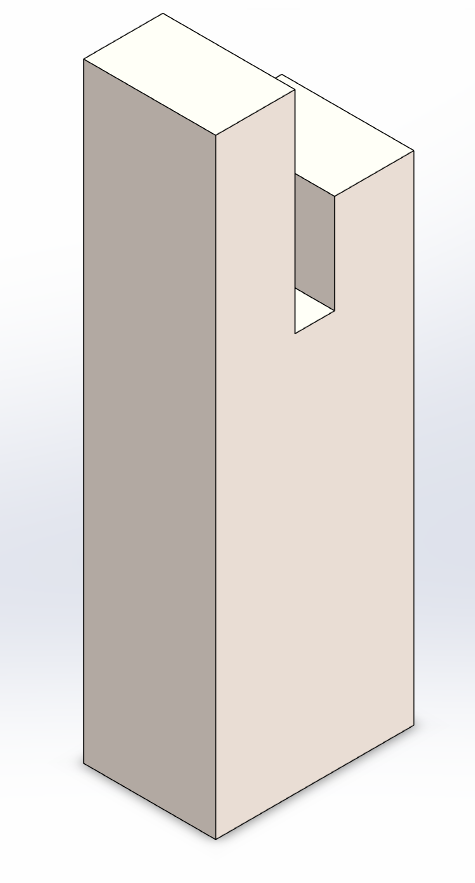
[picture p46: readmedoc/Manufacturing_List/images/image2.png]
Broad Holder 2 |  | 3 | FDM 3D Printing | ABS
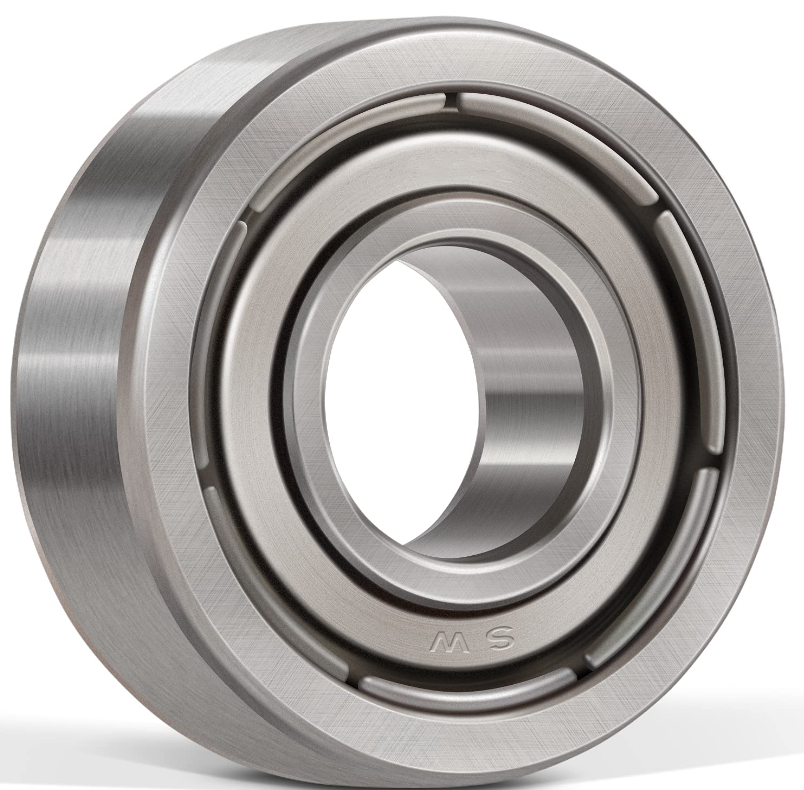
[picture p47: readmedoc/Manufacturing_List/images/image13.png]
Connection Bearing 3mm * 8mm * 4mm |  | 12 | Purchased From Amazon | Alloy Steel | $9.20 20 Pack 623ZZ Ball Bearing from Amazon (https://www.amazon.com/Bearing-Shielded-Bearings-Performance-Effective/dp/B092Z2QB6X)
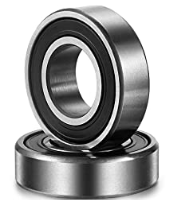
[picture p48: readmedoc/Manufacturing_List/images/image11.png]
Arm Bearing 8mm * 22mm * 7mm |  | 6 | Purchased From Amazon | Alloy Steel | 2*$10.99 4 Pack 608-2RS Ball Bearing from Amazon (https://www.amazon.com/Industrial-8x22x7mm-Bearings-Pre-Lubricated-Skateboards/dp/B09S5Z5J5L)
Screws (for capstan adjustment) size 4-40, 3/4" length |  | 3 | Purchased from Mcmaster-Carr Part ID: 91781A113 | 18-8 Stainless Steel | $6.78 per pack of 100
Pan Head Phillips Screws(for Hapkit installation),¼-20 3/4 |  | 12 | Purchased from Mcmaster-Carr Part ID:91772A540 | 18-8 Stainless Steel | $18.85 per pack of 50
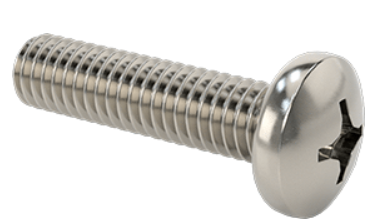
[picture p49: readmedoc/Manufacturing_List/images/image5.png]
Pan Head Phillips Screws(for bearing installation),M4 x 0.7mm Thread, 16mm Long |  | 12 | Purchased from Mcmaster-Carr Part ID:92000A226 | 18-8 Stainless Steel | $10.85 per pack of 50
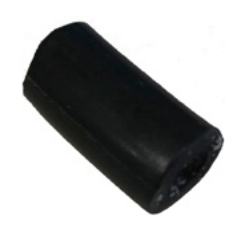
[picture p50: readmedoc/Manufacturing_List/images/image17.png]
Neoprene tubing, 1/4" inner diameter, 3/8" outer diameter, cut to 3/4" length |  | 3 | Purchased from Mcmaster-Carr Part ID:51075K27 | Neoprene | $12.2 for a 10'-long tube ($1.22 per foot)
Bearing: SAE 863 bronze flanged sleeve bearing |  | 3 | Purchased from Mcmaster-Carr Part ID: 2938T3 | 863 Iron-Copper | 3*$0.92
Stainless Steel Thread-Locking Shoulder Screw, 1/4" Diameter x 5/8" Long Shoulder, 10-24 Thread |  | 3 | Purchased from Mcmaster-Carr Part ID: 90311A144 | Stainless Steel | 3*$6.01
Shaft collar |  | 3 | Purchased from Mcmaster-Carr Part ID: 9414T6 | Black-oxide steel | 3*$1.55
Screws for the Motor |  | 6 | Purchased from Mcmaster-Carr Part ID: 91735A104 | 316 Stainless Steel | $4.59 For a Pack of 50
Washers for motor |  | 6 | Purchased from Mcmaster-Carr Part ID: 92150A101 | Nylon Plastic | $10.20 For a Pack of 100
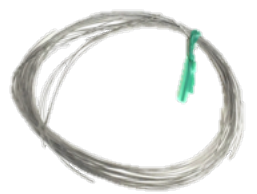
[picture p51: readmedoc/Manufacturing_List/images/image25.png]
Nylon Coated Stainless Steel Wire Rope |  | 3 | Purchased from Mcmaster-Carr Part ID: 8930T16 | 18-8 Stainless Steel | $10.00 For 25 feet
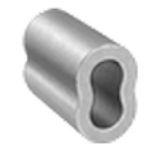
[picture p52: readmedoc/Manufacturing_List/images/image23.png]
Zinc - Plated Copper Oval Compression Sleeve |  | 3 | Purchased from Mcmaster-Carr Part ID: 3898T29 | Zinc-Plated Copper | $2.63 For a Pack of 50
Zinc - Plated Steel Machine Screw Hex Nut |  | 3 | Purchased from Mcmaster-Carr Part ID: 90480A005 | Zinc-Plated Steel | $1.05 For a Pack of 100
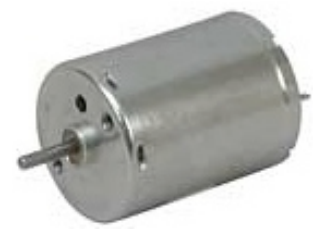
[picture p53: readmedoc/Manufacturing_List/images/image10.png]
Motor |  | 3 | Purchased from Jameco Part ID: 238473 | Motor | 3*$5.95
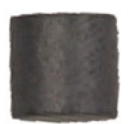
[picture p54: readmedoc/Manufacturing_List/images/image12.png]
Magnet |  | 3 | Purchased from Jameco Part ID: 57295K73 | Alnico | 3*$2.38
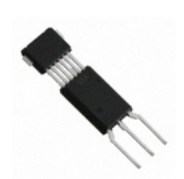
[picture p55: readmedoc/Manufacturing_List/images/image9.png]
Magnetoresistive sensor |  | 3 | Purchased from DigiKey PartID: 568-8399-1-ND | Magnet Sensor | 3*$6.73
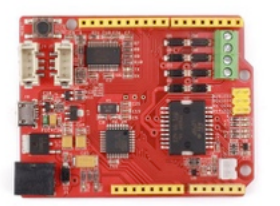
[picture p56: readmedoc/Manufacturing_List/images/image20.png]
Hapkit board |  | 3 | Purchased from Seeed Studio Part ID :KIT04300M | Hapkit Board | 3*$35
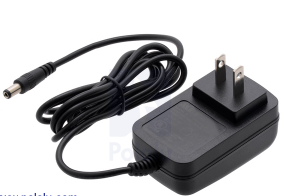
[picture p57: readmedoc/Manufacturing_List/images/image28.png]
Power supply for Hapkit board |  | 3 | Purchased from Pololu Part ID: 1471 | Power Supply | 3*$7.95
Leads with alligator clips on both ends |  | 3 | Purchased from Mouser Part ID: 474-CAB-14303 | Alligator Clips | $7.57
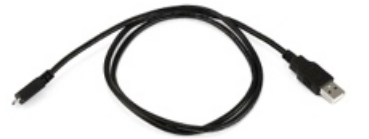
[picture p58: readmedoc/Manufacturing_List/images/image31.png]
USB cable for communication |  | 1 | Purchased from Monoprice Part ID: 4867 | Cable | $1.49

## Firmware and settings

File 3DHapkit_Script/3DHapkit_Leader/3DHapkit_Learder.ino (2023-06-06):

// 3D Hapkit Leader board Code
#include <Wire.h>

int pwmPin = 5; // PWM output pin for motor 1
int dirPin = 8; // direction output pin for motor 1

// Fastest transmission speed is 1/2 clock speed. On the Hapkit that's 16MHz clock speed. SPI can't be faster than 8MHz, would recommend 4MHz to be safe.

// On the atmega328p the SPI pins are on register B. 
// Change these assignments when using a different AVR processor.
#define DDR_SPI        DDRB
#define PORT_SPI       PORTB
#define DD_SCK         PB5
#define DD_LIFO        PB4 // This document uses Leader-Follower terminology
#define DD_LOFI        PB3
#define DD_SS          PB2 // This is the follower's chip select. 
#define DD_SS_INT      PCINT2 // When changing the follower CS make sure to change its interrupt vector and mask register too
#define DD_SS_INT_MSK  PCMSK0

#define DDR_FOLLOW_CS  DDRD // Data direction register for Port D, the register that both chip select pins sit on
#define FOLLOW_CS_PORT PORTD // Data register for Port D
#define F1_CS          PD7 // This is the chip select pin for the leader to select follower 1
#define F2_CS          PD6 // This is the chip select pin for the leader to select follower 2

int sensorPosPin = A2; // input pin for MR sensor

// Position tracking variables
int updatedPos = 0;     // keeps track of the latest updated value of the MR sensor reading
int rawPos = 0;         // current raw reading from MR sensor
int lastRawPos = 0;     // last raw reading from MR sensor
int lastLastRawPos = 0; // last last raw reading from MR sensor
int flipNumber = 0;     // keeps track of the number of flips over the 180deg mark
int tempOffset = 0;
int rawDiff = 0;
int lastRawDiff = 0;
int rawOffset = 0;
int lastRawOffset = 0;
const int flipThresh = 700;  // threshold to determine whether or not a flip over the 180 degree mark occurred
boolean flipped = false;
double OFFSET = 980;
double OFFSET_NEG = 15;
uint8_t dir = 0;
bool new_data = false;
double R = 95;
double r = 54.45;
double l1 = 80;
double l2 = 170;
int handle_pos[3];
double handle_angle[3];
double ts;
int zWallPosintion = 130;
int zWallThick = 10;
int nBallRadius = 10;
int nHoleRadius = 20;
int nCirleCenter[2][2];
// Kinematics variables
double xh = 0;           // position of the handle [m]
double theta_s = 0;      // Angle of the sector pulley in deg
double xh_prev;          // Distance of the handle at previous time step
double xh_prev2;
double dxh;              // Velocity of the handle
double dxh_prev;
double dxh_prev2;
double dxh_filt;         // Filtered velocity of the handle
double dxh_filt_prev;
double dxh_filt_prev2;
double force = 0;           // force at the handle
double duty[3];
int output = 0;
double Tp = 0;              // torque of the motor pulley

double rp = 0.005;   //[m]
double rs = 0.074;   //[m]
double rh = 0.090;
double dTmp =  rh * rp / (rs*0.03);  

bool bSerial =false;

#define PROCESSING 1 

void setup() {
  Wire.begin();        
  Serial.begin(115200);  
  
   #ifndef PROCESSING 
    Serial.println("Initialized Leader");
   #endif 
  delay(5000); //Give follower some time to come up.
  duty[0] = 0;  duty[1] = 0;  duty[2] = 0; 
    
// Input pins
  pinMode(sensorPosPin, INPUT); // set MR sensor pin to be an input
   
  // Output pins
  pinMode(pwmPin, OUTPUT);  // PWM pin for motor A
  pinMode(dirPin, OUTPUT);  // dir pin for motor A
  
 setPwmFrequency(pwmPin,1);  
 // Initialize motor 
  analogWrite(pwmPin, 0);     // set to not be spinning (0/255)
  digitalWrite(dirPin, LOW);  // set direction
  
  // Initialize position valiables
  lastLastRawPos = analogRead(sensorPosPin);
  lastRawPos = analogRead(sensorPosPin);
  flipNumber = 0;
  
  handle_pos[0] = 0; handle_pos[1] = 0; handle_pos[2] = 0;
   
  cli();
   
  TCCR1A = 0;
  TCCR1B = 0;
  TCNT1  = 0;

  OCR1A = 40;// = (16*10^6)/(50*1024) - 1 (must be <65536) 
  TCCR1B |= (1 << WGM12);
  TCCR1B |= (1 << CS12)| (1 << CS10);
  TIMSK1 |= (1 << OCIE1A);   

  nCirleCenter[0][0] = -20; 
  nCirleCenter[0][1] = -20; 
  nCirleCenter[1][0] = 20; 
  nCirleCenter[1][1] = 20;   
    
  sei();
  #ifdef PROCESSING
  establishContact();  // send a byte to establish contact until Processing responds 
  #endif
}
 
ISR(TIMER1_COMPA_vect)
{   
   ts = getAngle();
}

int dCCCC = (nHoleRadius+nBallRadius)*(nHoleRadius+nBallRadius); 

bool bIntersectCirle(double* b)
{
    bool bFlag = false;
    for(int i = 0; i < 3; i++)
    {
       // if(fabs(b[1]-nCirleCenter[i][0]) > nHoleRadius+nBallRadius);  
       double distace =  (b[1]-nCirleCenter[i][0])*(b[1]-nCirleCenter[i][0])+ (b[0]-nCirleCenter[i][1])*(b[01]-nCirleCenter[i][1]);
       if(distace < dCCCC) 
       {
           return true;
       }
    }
    return false; 
}

int getDisCircle2Circle(double* b)
{
    for(int i = 0; i < 2; i++)
    {
       // if(fabs(b[1]-nCirleCenter[i][0]) > nHoleRadius+nBallRadius);  
       double distace =  (b[1]-nCirleCenter[i][0])*(b[1]-nCirleCenter[i][0])+ (b[0]-nCirleCenter[i][1])*(b[0]-nCirleCenter[i][1]);
       if(distace < dCCCC) 
       {
           return sqrt(distace);
       }
    }
    return 1000;
}

int GetfollowerAngle(int nfollowerIndex)
{
    Wire.requestFrom(nfollowerIndex, 4);    // request 6 bytes from follower device #8
    int num = 0;
    int input = 0;
    while (Wire.available() && num < 4) { // follower may send less than requested
        byte c = Wire.read(); // receive a byte as character
        if(num == 0)
          input |= c;
        else if (num == 1)
          input |= (c<<8);
         else if (num == 2)
          input |= (c<<16);
        else if (num == 3)
           input |= (c<<24);
        num++;
    } 
    return input; 
}

void SendForce2follower(int nfollowerIndex,int out)
{   
    Wire.beginTransmission(nfollowerIndex); // transmit to device #8
    byte a[4];
    //int n = (output>=0? output:-output);     
    a[0] = out&0xFF; a[1] = (out>>8)&0xFF; a[2] = (out>>16)&0xFF; a[3] = (out>>24)&0xFF; 
    Wire.write(a,4);
    Wire.endTransmission();    // stop transmitting
}
  
void loop()
{   
  handle_angle[1] = GetfollowerAngle(8)/10.0; 
  delay(20);
  handle_angle[2] = GetfollowerAngle(12)/10.0; 

  #ifdef PROCESSING 
  if (Serial.available() > 0) 
  #endif
  {
     #ifdef PROCESSING
     int inByte = Serial.read();
     #endif       
 
     double RealAngle[3]; 
     RealAngle[0] = 110-ts; 
     RealAngle[1] = 112-handle_angle[1];
     RealAngle[2] = 112-handle_angle[2];
    
     double b[3];    
     forward(RealAngle, b);  
     handle_pos[0] = b[1]*10;handle_pos[1] = b[0]*10;handle_pos[2] = -b[2]*10;
  
     ////// //////  force
       
    xh = -((-b[2]-nBallRadius)-zWallPosintion-zWallThick/2)/1000.0;  
   
    bool bInverst = false;
    if(xh > (nBallRadius+zWallThick/2)/1000.0) bInverst = true;  

    if(xh < 0.0 || xh > 0.002*(nBallRadius+zWallThick/2)) force = 0;
    else   // Enabling a Virtual Wall
    { 
        int distanceCC = getDisCircle2Circle(b);                  
        if(distanceCC <= nBallRadius) force = 0;          
        else
        {
           if (bInverst) // virtual wall force feedback rendering
            {              
              force = 100 * fabs((2*nBallRadius+zWallThick)/1000.0-xh);
            }
            else   // force without the damping when exiting
            {
              force = 150 * (xh);
            }                        
        }       
    }     
    if(force > 4.5) force = 4.5;  // max fore = 4.9
    
    #ifndef PROCESSING 
     Serial.print("xh: ");
     Serial.print(xh*1000);    
     Serial.print(" dxh_filt: ");
     Serial.print(dxh_filt);
     Serial.print(" force: ");
     Serial.print(force);
   #endif
   
    double Tp = force * dTmp;//rh * rp / (rs*0.03);  
  
    // Determine correct direction for motor torque
    if(force > 0) { 
      digitalWrite(dirPin, bInverst?LOW:HIGH);
    } else {
      digitalWrite(dirPin, bInverst?HIGH:LOW);
    }
  
    // Compute the duty cycle required to generate Tp (torque at the motor pulley)
   
    //duty[0] = sqrt(abs(Tp)/0.03);
    duty[0] = sqrt(abs(Tp));
    
    #ifndef PROCESSING 
      Serial.print(" Tp: ");
      Serial.print(Tp);
   #endif 
   
    // Make sure the duty cycle is between 0 and 100%
    if (duty[0] > 1) {            
      duty[0] = 1;
    } else if (duty[0] < 0) { 
      duty[0] = 0;
    }  
    output = (int)(duty[0]* 255);   // convert duty cycle to output signal
    analogWrite(pwmPin,output);  // output the signal
  
    #ifndef PROCESSING 
      Serial.print(" output: ");
      Serial.print(output);
    #endif 
    
     if(force > 0) { 
       SendForce2follower(8,bInverst?-output:output);
       delay(20);
       SendForce2follower(12,bInverst?-output:output);
        
    } else {
       SendForce2follower(8,bInverst?output:-output);
       delay(20);
       SendForce2follower(12,bInverst?output:-output);  
    }
   
  
    ////////////////////   
      
      #ifdef PROCESSING 
          byte sign[2]; sign[0] = handle_pos[0]>=0?1:0; sign[1] = handle_pos[1]>=0?1:0;
          handle_pos[0] = fabs( handle_pos[0]); handle_pos[1] = fabs( handle_pos[1]);
          //handle_pos[0] = 10; handle_pos[1] = 100; handle_pos[2] = 300;
          Serial.write(handle_pos[0]&0xFF);  Serial.write((handle_pos[0]>>8)&0xFF); Serial.write((handle_pos[0]>>16)&0xFF); Serial.write((handle_pos[0]>>24)&0xFF); 
          Serial.write(handle_pos[1]&0xFF);  Serial.write((handle_pos[1]>>8)&0xFF); Serial.write((handle_pos[1]>>16)&0xFF); Serial.write((handle_pos[1]>>24)&0xFF); 
          Serial.write(handle_pos[2]&0xFF);  Serial.write((handle_pos[2]>>8)&0xFF); Serial.write((handle_pos[2]>>16)&0xFF); Serial.write((handle_pos[2]>>24)&0xFF);      
           Serial.write(sign[0]); Serial.write(sign[1]);         
       #else   
             
        Serial.print(" pos1: ");
        Serial.print(RealAngle[0]);
        Serial.print("  pos2: ");
        Serial.print(RealAngle[1]); 
        Serial.print("  pos3: ");
        Serial.print(RealAngle[2]);
        
        Serial.print(" x: ");
        Serial.print(handle_pos[0]/10.0);
        Serial.print(" y: ");
        Serial.print(handle_pos[1]/10.0);
        Serial.print(" z: ");
        Serial.println(handle_pos[2]/10.0);
      #endif      
   }            
}

double getAngle() 
{
  //*************************************************************
  //*** Section 1. Compute position in counts (do not change) ***  
  //*************************************************************
  
  // Get voltage output by MR sensor
  rawPos = analogRead(sensorPosPin);  //current raw position from MR sensor
  
  // Calculate differences between subsequent MR sensor readings
  rawDiff = rawPos - lastRawPos;          //difference btwn current raw position and last raw position
  lastRawDiff = rawPos - lastLastRawPos;  //difference btwn current raw position and last last raw position
  rawOffset = abs(rawDiff);
  lastRawOffset = abs(lastRawDiff);
  
  // Update position record-keeping vairables
  lastLastRawPos = lastRawPos;
  lastRawPos = rawPos;
  
  // Keep track of flips over 180 degrees
  if((lastRawOffset > flipThresh) && (!flipped)) { // enter this anytime the last offset is greater than the flip threshold AND it has not just flipped
    if(lastRawDiff > 0) {        // check to see which direction the drive wheel was turning
      flipNumber--;              // cw rotation 
    } else {                     // if(rawDiff < 0)
      flipNumber++;              // ccw rotation
    }
    flipped = true;            // set boolean so that the next time through the loop won't trigger a flip
  } else {                        // anytime no flip has occurred
    flipped = false;
  }
  updatedPos = rawPos + flipNumber*OFFSET; // need to update pos based on what most recent offset is
  //Serial.println(flipNumber);
  // Serial.println(updatedPos);

  //************************************************************
  //** Section 2. Compute position in meters *******************
  //************************************************************

  // Define kinematic parameters you may need
  double rh = 0.090;   //[m]
  // Step B.1: print updatedPos via serial monitor
  
  // Step B.2:
  double ts =  0.0111*updatedPos - 1.905;// Compute the angle of the sector pulley (ts) in degrees based on updatedPos
  return ts; 
}
// forward kinematics for 3D hapkit
void forward(double* angIn, double* pos)
{
  double ang[3];
  ang[0] = angIn[0] * PI / 180;
  ang[1] = angIn[1] * PI / 180;
  ang[2] = angIn[2] * PI / 180;
  double a1 = R + l1 * sin(ang[0]) - r;
  double b1 = 0;
  double c1 = l1 * cos(ang[0]);
  double a2 = -(R + l1 * sin(ang[1]) - r) / 2;
  double b2 = sqrt(3) * (R + l1 * sin(ang[1]) - r) / 2;
  double c2 = l1 * cos(ang[1]);
  double a3 = -(R + l1 * sin(ang[2]) - r) / 2;
  double b3 = -sqrt(3) * (R + l1 * sin(ang[2]) - r) / 2;
  double c3 = l1 * cos(ang[2]);
  double a12 = a2 - a1;
  double c12 = c2 - c1;
  double d1 = (pow(a2, 2) - pow(a1, 2) + pow(c2, 2) - pow(c1, 2) + pow(b2, 2)) / 2;
  double a13 = a3 - a1;
  double c13 = c3 - c1;
  double d2 = (pow(a3, 2) - pow(a1, 2) + pow(c3, 2) - pow(c1, 2) + pow(b3, 2)) / 2;
  double e1 = (b3 * c12 - b2 * c13) / (b3 * a12 - b2 * a13);
  double f1 = (b3 * d1 - b2 * d2) / (b3 * a12 - b2 * a13);
  double e2 = (a13 * c12 - a12 * c13) / (a13 * b2 - a12 * b3);
  double f2 = (a13 * d1 - a12 * d2) / (a12 * b2 - a12 * b3);
  double a = pow(e1, 2) + pow(e2, 2) + 1;
  double b = 2 * e1 * f1 - 2 * e1 * a1 + 2 * e2 * f2 + 2 * c1;
  double c = pow(f2, 2) + pow((a1 - f1), 2) + pow(c1, 2) - pow(l2, 2);
  double bb = b * b - 4 * a * c;
  double aa = sqrt(b * b - 4 * a * c);
  pos[2] = (-b - sqrt(b * b - 4 * a * c)) / (2 * a);
  pos[0] = e1 * pos[2] + f1;
  pos[1] = e2 * pos[2] + f2;
  pos[1] = -pos[1] ;
  return 0;
}

// --------------------------------------------------------------
// Function to set PWM Freq -- DO NOT EDIT
// --------------------------------------------------------------
void setPwmFrequency(int pin, int divisor) {
  byte mode;
  if(pin == 5 || pin == 6 || pin == 9 || pin == 10) {
    switch(divisor) {
      case 1: mode = 0x01; break;
      case 8: mode = 0x02; break;
      case 64: mode = 0x03; break;
      case 256: mode = 0x04; break;
      case 1024: mode = 0x05; break;
      default: return;
    }
    if(pin == 5 || pin == 6) {
      TCCR0B = TCCR0B & 0b11111000 | mode;
    } else {
      TCCR1B = TCCR1B & 0b11111000 | mode;
    }
  } else if(pin == 3 || pin == 11) {
    switch(divisor) {
      case 1: mode = 0x01; break;
      case 8: mode = 0x02; break;
      case 32: mode = 0x03; break;
      case 64: mode = 0x04; break;
      case 128: mode = 0x05; break;
      case 256: mode = 0x06; break;
      case 1024: mode = 0x7; break;
      default: return;
    }
    TCCR2B = TCCR2B & 0b11111000 | mode;
  }
}


void establishContact() {
 while (Serial.available() <= 0) {
      Serial.write('A');   // send a capital A
      delay(1000);
      bSerial = true;

  }
}

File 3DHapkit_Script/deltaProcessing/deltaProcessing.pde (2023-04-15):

import processing.serial.*;
Serial myPort;         
int valr;            

 
 // Press 'w' to start wiggling, space to restore
// original positions.

int zWallThick = 10;
int[][] nCirleCenter = new int[2][2];  
float dWllPos = 130;
float cubeSize = 320;
int circleRad = 20; 
int circleBig = 20;  
int circleRes = 40;
float noiseMag = 1;
float x,y,z;
int[] serialInArray = new int[14];    // Where we'll put what we receive
int serialCount = 0;                 // A count of how many bytes we receive
int xpos, ypos,zpos;                 // Starting position of the ball
boolean firstContact = false;        // Whether we've heard from the microcontroller
boolean locked = false;  
float xOffset = 0.0; 
float yOffset = 0.0; 
float bx;
float by;
boolean wiggling = false;

int[] origin = new int[3];
PShape face2; 
PShape planet2;
PImage surftex2;
PShape cube;

void setup() {

  size(1424, 800, P3D);    
  myPort = new Serial(this, "com5", 115200);
  nCirleCenter[0][0] = -20; 
  nCirleCenter[0][1] = -20; 
  nCirleCenter[1][0] = 20; 
  nCirleCenter[1][1] = 20; 
  
  createCube();  
  stroke(0,255,0);
  planet2 = createShape(SPHERE, circleRad/2); 
  x = y = z = 0;
  //face2 = createShape();   
  //createFaceWithHole2(face2);
}

void draw() {
  
  background(0);
  translate(width/2, height/2);
 
  rotateX(50 * 0.01f);
  rotateY(-10 * 0.01f);
  
  rotateY(xOffset/180*3.1415);
  rotateX(yOffset/180*3.1415);
  
   noStroke();
   //sphereDetail(10);
   
   stroke(255, 0, 0);
   
  origin[0] = -170; 
  origin[1] = -170;
  origin[2] = -170;
  
  int lineLength = 450;
   
   line( origin[0],  origin[1],  origin[2], origin[0]+lineLength, origin[1],  origin[2]);
   line( origin[0],  origin[1],  origin[2], origin[0], origin[1]+lineLength,  origin[2]);
   line( origin[0],  origin[1],  origin[2], origin[0],  origin[1], origin[2]+lineLength);
   
   stroke(0, 255, 0);
   textSize(36);
   text("X",origin[0]+lineLength, origin[1],  origin[2]); //<>//
   text("Y", origin[0], origin[1]+lineLength,  origin[2]);
   text("Z",  origin[2],origin[1], origin[2]+lineLength);
 
 
  //shape(face2);
  shape(cube);
  
  fill(255, 0, 0); 
 
  pushMatrix();
 // rotateY(PI * frameCount / 500);
  translate(x,y,z);  
  shape(planet2);
 // planet2.stroke(255,255, 0);
  popMatrix();  
}

int dCCCC = (circleRad+circleRad/2)*(circleRad+circleRad/2); 

int getDisCircle2Circle(float x,float y)
{
    for(int i = 0; i < 2; i++)
    {        
      float distace =  (x-nCirleCenter[i][0])*(x-nCirleCenter[i][0])+ (y-nCirleCenter[i][1])*(y-nCirleCenter[i][1]);
      if( distace <  (circleRad/2)*(circleRad/2))
       {
           return int(sqrt(distace));
       }
    }
    return 1000;
}

void serialEvent(Serial myPort) {
  // read a byte from the serial port:
  int inByte = myPort.read();
  // if this is the first byte received, and it's an A,
  // clear the serial buffer and note that you've
  // had first contact from the microcontroller. 
  // Otherwise, add the incoming byte to the array:
  if (firstContact == false) {
    if (inByte == 'A') { 
      myPort.clear();          // clear the serial port buffer
      firstContact = true;     // you've had first contact from the microcontroller
      myPort.write('A');       // ask for more
    } 
  } 
  else 
  {
    // Add the latest byte from the serial port to array:
    serialInArray[serialCount] = inByte;
    serialCount++;
   
    // If we have 12 bytes:
    if (serialCount > 13 ) {
      xpos=ypos=zpos=0;
      xpos = serialInArray[0]; xpos |= (serialInArray[1]<<8); xpos |= (serialInArray[2]<<16); xpos |= (serialInArray[3]<<24);
      ypos = serialInArray[4]; ypos |= (serialInArray[5]<<8); ypos |= (serialInArray[6]<<16); ypos |= (serialInArray[7]<<24);
      zpos = serialInArray[8]; zpos |= (serialInArray[9]<<8); zpos |= (serialInArray[10]<<16);zpos |= (serialInArray[11]<<24);          
      //x = -x;
      x = xpos/10.0;
      y = ypos/10.0;
      z = zpos/10.0;
      if(serialInArray[12] == 0) x = -x;
      if(serialInArray[13] == 0) y = -y;
      
      println(x + "\t" + y + "\t" + z);
      
      int distanceCC = getDisCircle2Circle(x,y);
      int bInCircle = 0;              
      if(distanceCC <= dCCCC) bInCircle = 1; 
      if(bInCircle == 0)
      {
         if(z <= dWllPos+circleRad/2 &&  z >= dWllPos+zWallThick-circleRad/2)
         // if(z <= 140 &&  z >= 125)
          {
                z = dWllPos+circleRad/2;
          }
          else if(z >= dWllPos-zWallThick-circleRad/2 &&  z <= dWllPos-circleRad/2)
          //else if(z >= 110 &&  z <= 125)
          {
                z = dWllPos-zWallThick-circleRad/2;
          }
      } 
      //println(bInCircle + "\t" + z + "\t" );
     
      // print the values (for debugging purposes only):
     // println(x + "\t" + y + "\t" + z);

      // Send a capital A to request new sensor readings:
      myPort.write('A');
      // Reset serialCount:
      serialCount = 0;
    }
  }
}

void createFaceWithHole2(PShape face) {
  face.beginShape(POLYGON);
  face.stroke(0, 0, 255);
  face.fill(125);

  // Draw main shape Clockwise
  face.vertex(-cubeSize/2, -cubeSize/2, dWllPos);
  face.vertex(+cubeSize/2, -cubeSize/2, dWllPos);
  face.vertex(+cubeSize/2, +cubeSize/2, dWllPos);
  face.vertex(-cubeSize / 2, +cubeSize / 2, dWllPos);

  // Draw contour (hole) Counter-Clockwise
  face.beginContour();
  for (int i = 0; i < circleRes; i++) {
    float angle = TWO_PI * i / circleRes;
    float x = nCirleCenter[0][0]+circleRad * sin(angle);
    float y = nCirleCenter[0][1]+circleRad * cos(angle);
    float z = dWllPos;
    face.vertex(x, y, z);
  }
  face.endContour();
  
  face.beginContour();
  for (int i = 0; i < circleRes; i++) {
    float angle = TWO_PI * i / circleRes;
    float x = nCirleCenter[1][0]+circleRad * sin(angle);
    float y = nCirleCenter[1][0]+circleRad * cos(angle);
    float z = dWllPos;
    face.vertex(x, y, z);
  }
  face.endContour();
  
  face.endShape(CLOSE);
}
 
void createCube() 
{  
  cube = createShape(GROUP);  
  PShape face;
  // Create all faces at front position
  for (int i = 0; i < 6; i++) {
    face = createShape();
    createFaceWithHole(face,i);
    cube.addChild(face);
  }

  // Rotate all the faces to their positions

  // Front face - already correct
  face = cube.getChild(0);

  // Back face
  face = cube.getChild(1); 
  face.translate(0,0,-zWallThick); 
  
  // Right face
  face = cube.getChild(2);  
  face.translate(0,0,0);
  
  // Left face
  face = cube.getChild(3);   
  face.translate(cubeSize,0,0);
  
  // Top face
  face = cube.getChild(4);
  
  // Bottom face
  face = cube.getChild(5);
  face.translate(0,cubeSize,0);
}
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

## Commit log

2023-06-03 Modified the tolerance
    [3D-Hapkit.SLDASM, LaserCut_Frame.SLDPRT, LaserCut_FrameX3.DXF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]
2023-06-05 Update the forward kinematics
